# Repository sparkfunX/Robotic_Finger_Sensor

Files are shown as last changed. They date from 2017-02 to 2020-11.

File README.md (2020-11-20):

Robotic Finger Sensor 
========================

Robotic Finger Sensor

Robotic Finger Sensor  

[*Robotic Finger Sensor (SPX-14200)*](https://www.sparkfun.com/products/14200)  

[*Robotic Finger Sensor v2 (SPX-14687)*](https://www.sparkfun.com/products/14687)

A robotic finger sensor capable of detecting very light touches. Uses the VCNL4040 IR distance sensor. 

Repository Contents
------------------

* **/Firmware** - Example Arduino sketch to demostrate how to read from the various sensors.
* **/Hardware** - All the Eagle PCB design files (.brd, .sch). MOld files are included as well. 

License Information
-------------------

This product is _**open source**_! 

Please review the LICENSE.md file for license information. 

If you have any questions or concerns on licensing, please contact technical support on our [SparkFun forums](https://forum.sparkfun.com/viewforum.php?f=152).

Distributed as-is; no warranty is given.

- Your friends at SparkFun.

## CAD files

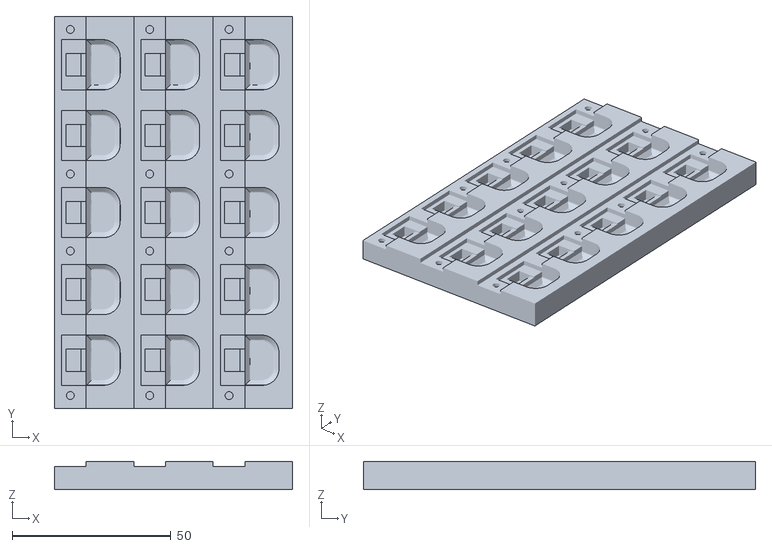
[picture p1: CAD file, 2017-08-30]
Hardware/MOLD/FingerMoldIceCubeProduction_Reduced_depth.stl
75.0 x 123.5 x 8.89

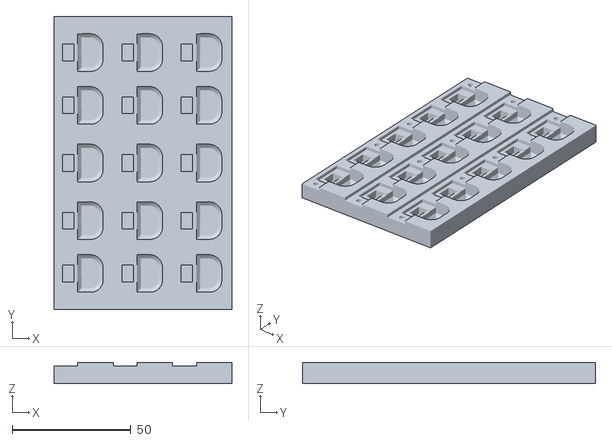
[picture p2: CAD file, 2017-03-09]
Hardware/MOLD/FingerMoldIceCubeProduction.stl
75.0 x 123.5 x 8.89

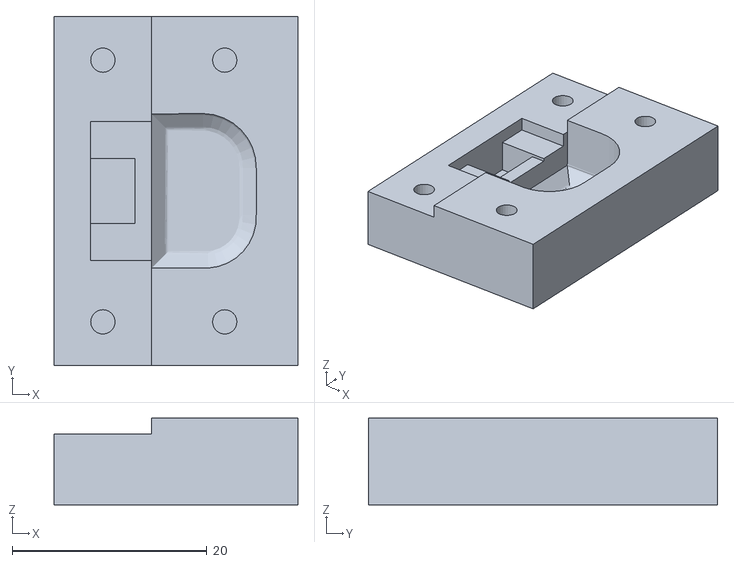
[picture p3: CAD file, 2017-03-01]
Hardware/MOLD/FingerMoldIceCube.stl
25.0 x 35.8 x 8.89

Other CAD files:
Hardware/MOLD/FingerMoldIceCube.skp
Hardware/MOLD/FingerMoldIceCubeProduction.skp
Hardware/MOLD/FingerMoldIceCubeProduction~.skp
Hardware/MOLD/FingerMoldIceCube~.skp

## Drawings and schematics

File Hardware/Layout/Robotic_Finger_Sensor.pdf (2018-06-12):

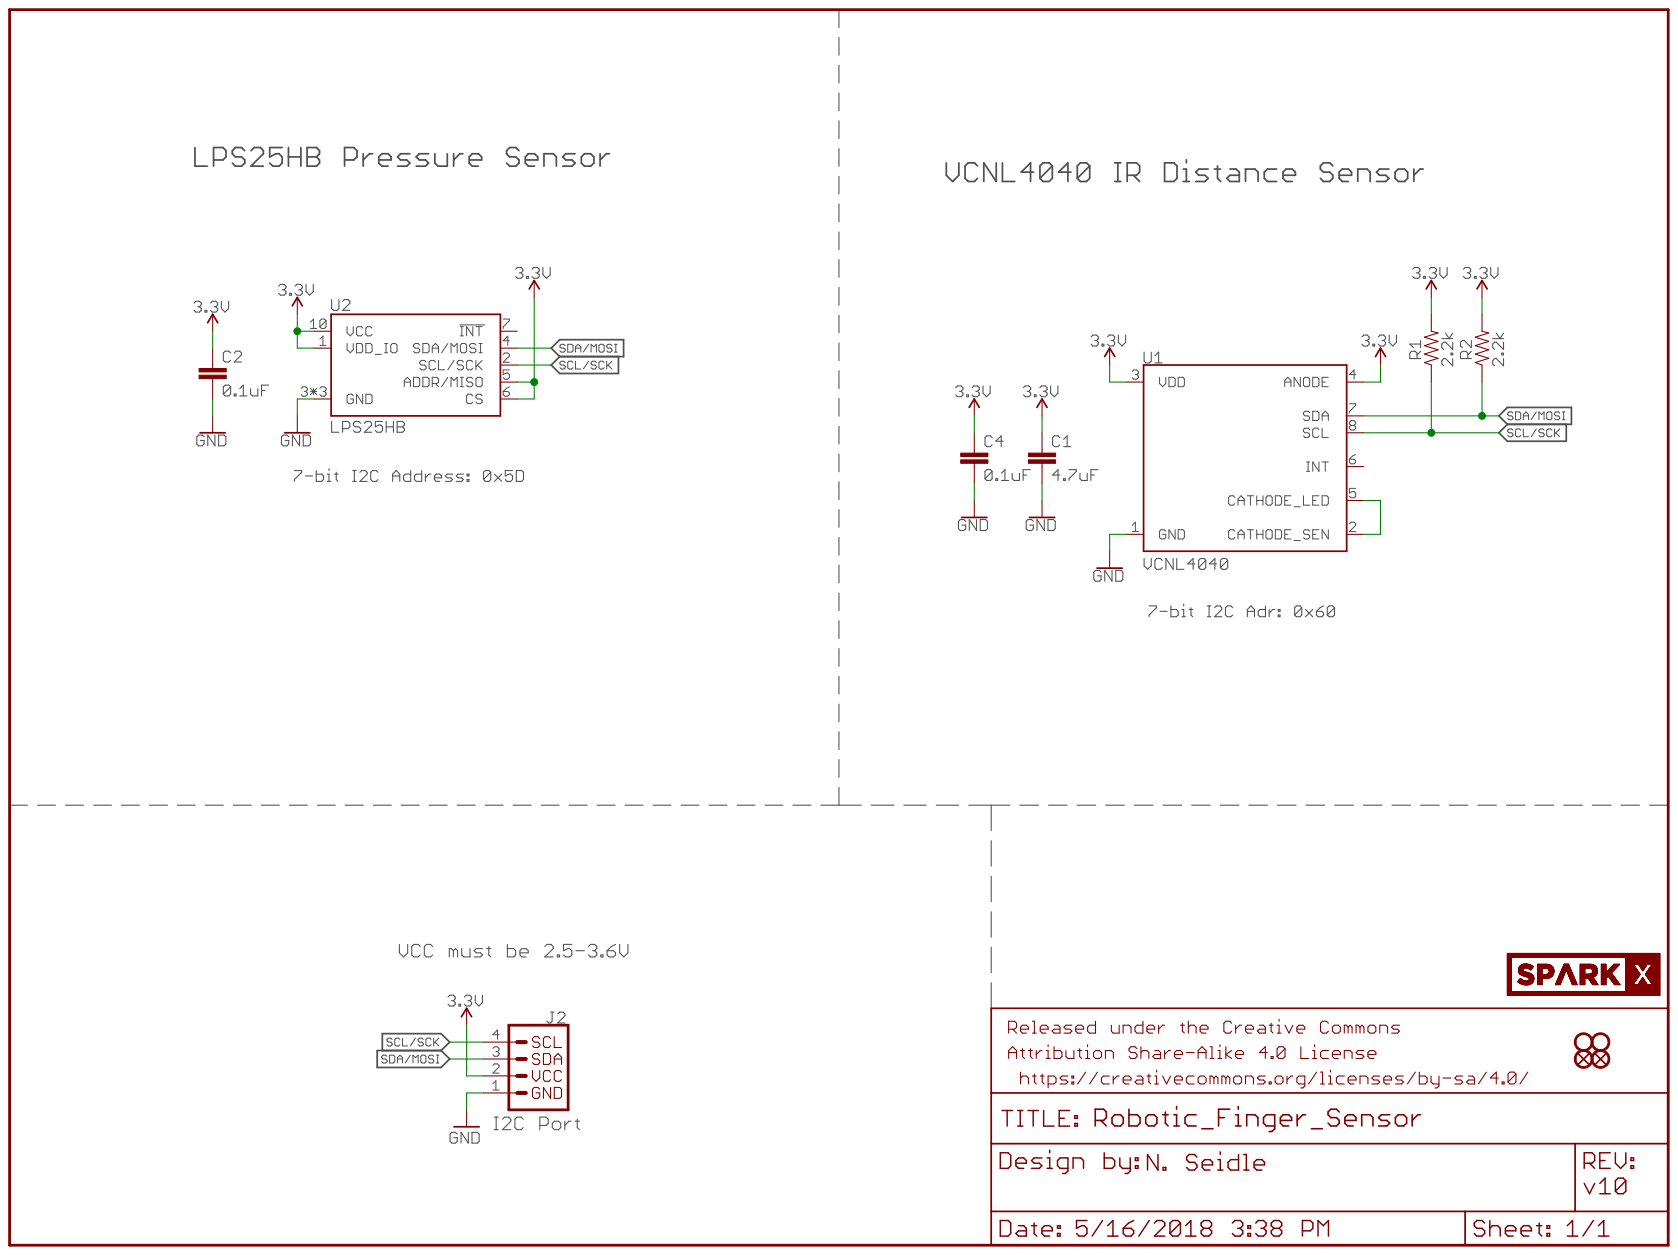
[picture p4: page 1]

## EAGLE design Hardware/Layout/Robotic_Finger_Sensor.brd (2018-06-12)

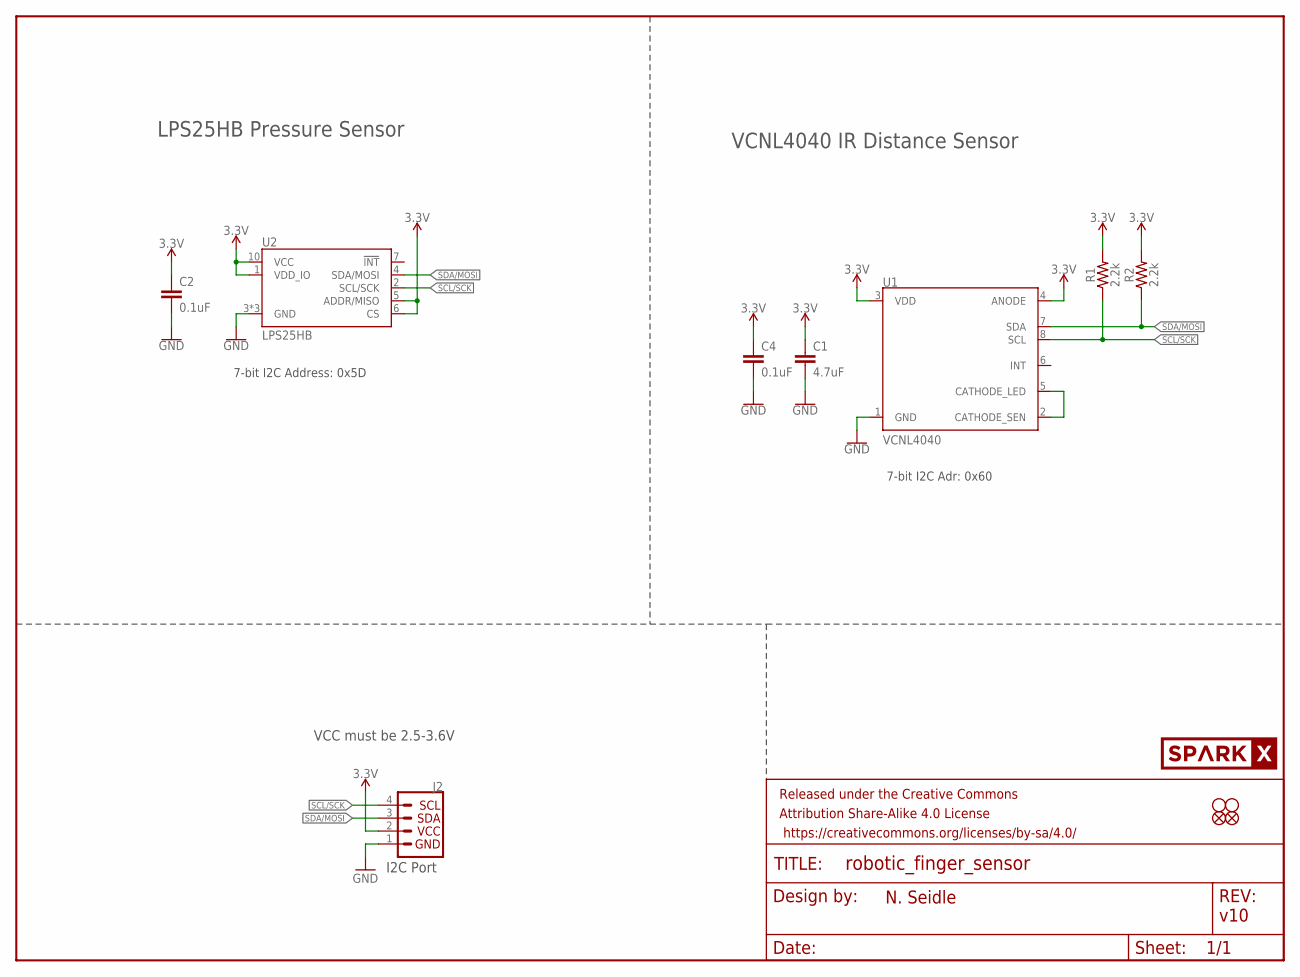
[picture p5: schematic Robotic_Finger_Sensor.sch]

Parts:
C1: 4.7uF; 0603
C2, C4: 0.1uF; 0603
FD1, FD2: FIDUCIALUFIDUCIAL; FIDUCIAL-MICRO
FRAME2: FRAME-LETTER; CREATIVE_COMMONS
J2: I2C_STANDARDJS-1MM; 1X04_1MM_RA
R1, R2: 2.2k; 0603
U1: VCNL4040
U2: LPS25HB
U$2: SPARKX-LOGO3; SPARKX-SMALL
U$3, U$4: STAND-OFF; STAND-OFF-#2

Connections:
3.3V: C1.1, C2.1, C4.1, J2.2 (VCC), R1.2, R2.2, U1.3 (VDD), U1.4 (ANODE), U2.1 (VDD_IO), U2.5 (ADDR/MISO), U2.6 (CS), U2.10 (VCC)
GND: C1.2, C2.2, C4.2, J2.1 (GND), U1.1 (GND), U2.3 (GND), U2.8 (GND), U2.9 (GND)
unnamed: U1.2 (CATHODE_SEN), U1.5 (CATHODE_LED)
SCL/SCK: J2.4 (SCL), R1.1, U1.8 (SCL), U2.2 (SCL/SCK)
SDA/MOSI: J2.3 (SDA), R2.1, U1.7 (SDA), U2.4 (SDA/MOSI)

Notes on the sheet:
v10
N. Seidle
VCNL4040 IR Distance Sensor
VCC must be 2.5-3.6V
I2C Port
7-bit I2C Adr: 0x60
LPS25HB Pressure Sensor
7-bit I2C Address: 0x5D

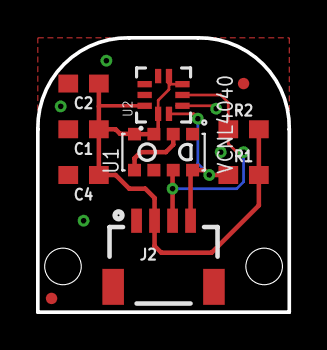
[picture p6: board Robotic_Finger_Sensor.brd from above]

Board: 2 copper layers, 14.0 x 15.2 mm, 18 parts (5 on the bottom side), 5 nets.

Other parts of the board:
U$6: ROBOTIC0
U$7: SENSOR2
U$9: FINGER0
U$11: (QWIIC)

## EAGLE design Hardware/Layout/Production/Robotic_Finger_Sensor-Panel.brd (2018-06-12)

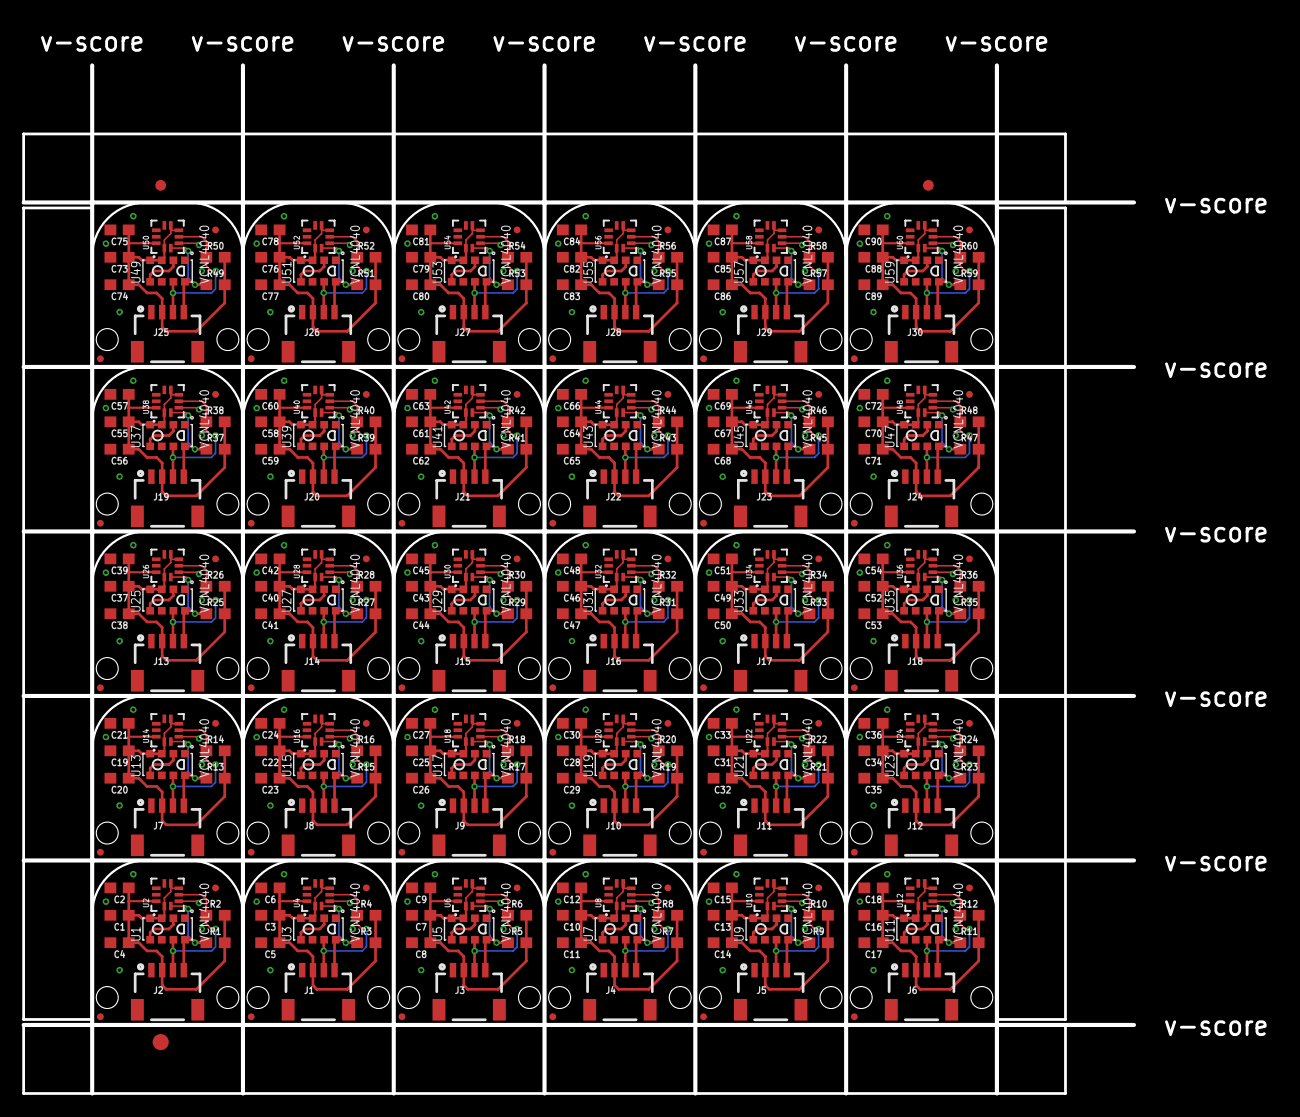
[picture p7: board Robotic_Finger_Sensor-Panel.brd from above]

Board: 2 copper layers, 102.9 x 95.2 mm, 513 parts (150 on the bottom side), 150 nets.

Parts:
C1, C3, C7, C10, C13, C16, C19, C22, C25, C28, C31, C34, C37, C40, C43, C46, C49, C52, C55, C58, C61, C64, C67, C70, C73, C76, C79, C82, C85, C88: 4.7uF; 0603
C2, C4, C5, C6, C8, C9, C11, C12, C14, C15, C17, C18, C20, C21, C23, C24, C26, C27, C29, C30, C32, C33, C35, C36, C38, C39, C41, C42, C44, C45, C47, C48, C50, C51, C53, C54, C56, C57, C59, C60, C62, C63, C65, C66, C68, C69, C71, C72, C74, C75, C77, C78, C80, C81, C83, C84, C86, C87, C89, C90: 0.1uF; 0603
E$1, E$2: FIDUCIAL-1X2
E$3: FIDUCIAL-1.5X3
FD1, FD2, FD3, FD4, FD5, FD6, FD7, FD8, FD9, FD10, FD11, FD12, FD13, FD14, FD15, FD16, FD17, FD18, FD19, FD20, FD21, FD22, FD23, FD24, FD25, FD26, FD27, FD28, FD29, FD30, FD31, FD32, FD33, FD34, FD35, FD36, FD37, FD38, FD39, FD40, FD41, FD42, FD43, FD44, FD45, FD46, FD47, FD48, FD49, FD50, FD51, FD52, FD53, FD54, FD55, FD56, FD57, FD58, FD59, FD60: FIDUCIALUFIDUCIAL; FIDUCIAL-MICRO
J1, J2, J3, J4, J5, J6, J7, J8, J9, J10, J11, J12, J13, J14, J15, J16, J17, J18, J19, J20, J21, J22, J23, J24, J25, J26, J27, J28, J29, J30: 1X04_1MM_RA
R1, R2, R3, R4, R5, R6, R7, R8, R9, R10, R11, R12, R13, R14, R15, R16, R17, R18, R19, R20, R21, R22, R23, R24, R25, R26, R27, R28, R29, R30, R31, R32, R33, R34, R35, R36, R37, R38, R39, R40, R41, R42, R43, R44, R45, R46, R47, R48, R49, R50, R51, R52, R53, R54, R55, R56, R57, R58, R59, R60: 2.2k; 0603
U1, U3, U5, U7, U9, U11, U13, U15, U17, U19, U21, U23, U25, U27, U29, U31, U33, U35, U37, U39, U41, U43, U45, U47, U49, U51, U53, U55, U57, U59: VCNL4040
U2, U4, U6, U8, U10, U12, U14, U16, U18, U20, U22, U24, U26, U28, U30, U32, U34, U36, U38, U40, U42, U44, U46, U48, U50, U52, U54, U56, U58, U60: LPS25HB
U$1, U$2, U$15, U$22, U$29, U$36, U$43, U$50, U$57, U$64, U$71, U$78, U$85, U$92, U$99, U$106, U$113, U$120, U$127, U$134, U$141, U$148, U$155, U$162, U$169, U$176, U$183, U$190, U$197, U$204: SPARKX-LOGO3; SPARKX-SMALL
U$3, U$4, U$5, U$8, U$16, U$17, U$23, U$24, U$30, U$31, U$37, U$38, U$44, U$45, U$51, U$52, U$58, U$59, U$65, U$66, U$72, U$73, U$79, U$80, U$86, U$87, U$93, U$94, U$100, U$101, U$107, U$108, U$114, U$115, U$121, U$122, U$128, U$129, U$135, U$136, U$142, U$143, U$149, U$150, U$156, U$157, U$163, U$164, U$170, U$171, U$177, U$178, U$184, U$185, U$191, U$192, U$198, U$199, U$205, U$206: STAND-OFF; STAND-OFF-#2
U$6, U$12, U$19, U$26, U$33, U$40, U$47, U$54, U$61, U$68, U$75, U$82, U$89, U$96, U$103, U$110, U$117, U$124, U$131, U$138, U$145, U$152, U$159, U$166, U$173, U$180, U$187, U$194, U$201, U$208: ROBOTIC0
U$7, U$13, U$20, U$27, U$34, U$41, U$48, U$55, U$62, U$69, U$76, U$83, U$90, U$97, U$104, U$111, U$118, U$125, U$132, U$139, U$146, U$153, U$160, U$167, U$174, U$181, U$188, U$195, U$202, U$209: SENSOR2
U$9, U$14, U$21, U$28, U$35, U$42, U$49, U$56, U$63, U$70, U$77, U$84, U$91, U$98, U$105, U$112, U$119, U$126, U$133, U$140, U$147, U$154, U$161, U$168, U$175, U$182, U$189, U$196, U$203, U$210: FINGER0
U$10, U$11, U$18, U$25, U$32, U$39, U$46, U$53, U$60, U$67, U$74, U$81, U$88, U$95, U$102, U$109, U$116, U$123, U$130, U$137, U$144, U$151, U$158, U$165, U$172, U$179, U$186, U$193, U$200, U$207: (QWIIC)

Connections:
3.3V: C1.1, C2.1, C4.1, J2.2, R1.2, R2.2, U1.3, U1.4, U2.1, U2.5, U2.6, U2.10
3.3V1: C3.1, C5.1, C6.1, J1.2, R3.2, R4.2, U3.3, U3.4, U4.1, U4.5, U4.6, U4.10
3.3V2: C7.1, C8.1, C9.1, J3.2, R5.2, R6.2, U5.3, U5.4, U6.1, U6.5, U6.6, U6.10
3.3V3: C10.1, C11.1, C12.1, J4.2, R7.2, R8.2, U7.3, U7.4, U8.1, U8.5, U8.6, U8.10
3.3V4: C13.1, C14.1, C15.1, J5.2, R9.2, R10.2, U9.3, U9.4, U10.1, U10.5, U10.6, U10.10
3.3V5: C16.1, C17.1, C18.1, J6.2, R11.2, R12.2, U11.3, U11.4, U12.1, U12.5, U12.6, U12.10
3.3V6: C19.1, C20.1, C21.1, J7.2, R13.2, R14.2, U13.3, U13.4, U14.1, U14.5, U14.6, U14.10
3.3V7: C22.1, C23.1, C24.1, J8.2, R15.2, R16.2, U15.3, U15.4, U16.1, U16.5, U16.6, U16.10
3.3V8: C25.1, C26.1, C27.1, J9.2, R17.2, R18.2, U17.3, U17.4, U18.1, U18.5, U18.6, U18.10
3.3V9: C28.1, C29.1, C30.1, J10.2, R19.2, R20.2, U19.3, U19.4, U20.1, U20.5, U20.6, U20.10
3.3V10: C31.1, C32.1, C33.1, J11.2, R21.2, R22.2, U21.3, U21.4, U22.1, U22.5, U22.6, U22.10
3.3V11: C34.1, C35.1, C36.1, J12.2, R23.2, R24.2, U23.3, U23.4, U24.1, U24.5, U24.6, U24.10
3.3V12: C37.1, C38.1, C39.1, J13.2, R25.2, R26.2, U25.3, U25.4, U26.1, U26.5, U26.6, U26.10
3.3V13: C40.1, C41.1, C42.1, J14.2, R27.2, R28.2, U27.3, U27.4, U28.1, U28.5, U28.6, U28.10
3.3V14: C43.1, C44.1, C45.1, J15.2, R29.2, R30.2, U29.3, U29.4, U30.1, U30.5, U30.6, U30.10
3.3V15: C46.1, C47.1, C48.1, J16.2, R31.2, R32.2, U31.3, U31.4, U32.1, U32.5, U32.6, U32.10
3.3V16: C49.1, C50.1, C51.1, J17.2, R33.2, R34.2, U33.3, U33.4, U34.1, U34.5, U34.6, U34.10
3.3V17: C52.1, C53.1, C54.1, J18.2, R35.2, R36.2, U35.3, U35.4, U36.1, U36.5, U36.6, U36.10
3.3V18: C55.1, C56.1, C57.1, J19.2, R37.2, R38.2, U37.3, U37.4, U38.1, U38.5, U38.6, U38.10
3.3V19: C58.1, C59.1, C60.1, J20.2, R39.2, R40.2, U39.3, U39.4, U40.1, U40.5, U40.6, U40.10
3.3V20: C61.1, C62.1, C63.1, J21.2, R41.2, R42.2, U41.3, U41.4, U42.1, U42.5, U42.6, U42.10
3.3V21: C64.1, C65.1, C66.1, J22.2, R43.2, R44.2, U43.3, U43.4, U44.1, U44.5, U44.6, U44.10
3.3V22: C67.1, C68.1, C69.1, J23.2, R45.2, R46.2, U45.3, U45.4, U46.1, U46.5, U46.6, U46.10
3.3V23: C70.1, C71.1, C72.1, J24.2, R47.2, R48.2, U47.3, U47.4, U48.1, U48.5, U48.6, U48.10
3.3V24: C73.1, C74.1, C75.1, J25.2, R49.2, R50.2, U49.3, U49.4, U50.1, U50.5, U50.6, U50.10
3.3V25: C76.1, C77.1, C78.1, J26.2, R51.2, R52.2, U51.3, U51.4, U52.1, U52.5, U52.6, U52.10
3.3V26: C79.1, C80.1, C81.1, J27.2, R53.2, R54.2, U53.3, U53.4, U54.1, U54.5, U54.6, U54.10
3.3V27: C82.1, C83.1, C84.1, J28.2, R55.2, R56.2, U55.3, U55.4, U56.1, U56.5, U56.6, U56.10
3.3V28: C85.1, C86.1, C87.1, J29.2, R57.2, R58.2, U57.3, U57.4, U58.1, U58.5, U58.6, U58.10
3.3V29: C88.1, C89.1, C90.1, J30.2, R59.2, R60.2, U59.3, U59.4, U60.1, U60.5, U60.6, U60.10
GND: C1.2, C2.2, C4.2, J2.1, U1.1, U2.3, U2.8, U2.9
GND1: C3.2, C5.2, C6.2, J1.1, U3.1, U4.3, U4.8, U4.9
GND2: C7.2, C8.2, C9.2, J3.1, U5.1, U6.3, U6.8, U6.9
GND3: C10.2, C11.2, C12.2, J4.1, U7.1, U8.3, U8.8, U8.9
GND4: C13.2, C14.2, C15.2, J5.1, U9.1, U10.3, U10.8, U10.9
GND5: C16.2, C17.2, C18.2, J6.1, U11.1, U12.3, U12.8, U12.9
GND6: C19.2, C20.2, C21.2, J7.1, U13.1, U14.3, U14.8, U14.9
GND7: C22.2, C23.2, C24.2, J8.1, U15.1, U16.3, U16.8, U16.9
GND8: C25.2, C26.2, C27.2, J9.1, U17.1, U18.3, U18.8, U18.9
GND9: C28.2, C29.2, C30.2, J10.1, U19.1, U20.3, U20.8, U20.9
GND10: C31.2, C32.2, C33.2, J11.1, U21.1, U22.3, U22.8, U22.9
GND11: C34.2, C35.2, C36.2, J12.1, U23.1, U24.3, U24.8, U24.9
GND12: C37.2, C38.2, C39.2, J13.1, U25.1, U26.3, U26.8, U26.9
GND13: C40.2, C41.2, C42.2, J14.1, U27.1, U28.3, U28.8, U28.9
GND14: C43.2, C44.2, C45.2, J15.1, U29.1, U30.3, U30.8, U30.9
GND15: C46.2, C47.2, C48.2, J16.1, U31.1, U32.3, U32.8, U32.9
GND16: C49.2, C50.2, C51.2, J17.1, U33.1, U34.3, U34.8, U34.9
GND17: C52.2, C53.2, C54.2, J18.1, U35.1, U36.3, U36.8, U36.9
GND18: C55.2, C56.2, C57.2, J19.1, U37.1, U38.3, U38.8, U38.9
GND19: C58.2, C59.2, C60.2, J20.1, U39.1, U40.3, U40.8, U40.9
GND20: C61.2, C62.2, C63.2, J21.1, U41.1, U42.3, U42.8, U42.9
GND21: C64.2, C65.2, C66.2, J22.1, U43.1, U44.3, U44.8, U44.9
GND22: C67.2, C68.2, C69.2, J23.1, U45.1, U46.3, U46.8, U46.9
GND23: C70.2, C71.2, C72.2, J24.1, U47.1, U48.3, U48.8, U48.9
GND24: C73.2, C74.2, C75.2, J25.1, U49.1, U50.3, U50.8, U50.9
GND25: C76.2, C77.2, C78.2, J26.1, U51.1, U52.3, U52.8, U52.9
GND26: C79.2, C80.2, C81.2, J27.1, U53.1, U54.3, U54.8, U54.9
GND27: C82.2, C83.2, C84.2, J28.1, U55.1, U56.3, U56.8, U56.9
GND28: C85.2, C86.2, C87.2, J29.1, U57.1, U58.3, U58.8, U58.9
GND29: C88.2, C89.2, C90.2, J30.1, U59.1, U60.3, U60.8, U60.9
unnamed: U1.2, U1.5
unnamed: U3.2, U3.5
unnamed: U5.2, U5.5
unnamed: U7.2, U7.5
unnamed: U9.2, U9.5
unnamed: U11.2, U11.5
unnamed: U13.2, U13.5
unnamed: U15.2, U15.5
unnamed: U17.2, U17.5
unnamed: U19.2, U19.5
unnamed: U21.2, U21.5
unnamed: U23.2, U23.5
unnamed: U25.2, U25.5
unnamed: U27.2, U27.5
unnamed: U29.2, U29.5
unnamed: U31.2, U31.5
unnamed: U33.2, U33.5
unnamed: U35.2, U35.5
unnamed: U37.2, U37.5
unnamed: U39.2, U39.5
unnamed: U41.2, U41.5
unnamed: U43.2, U43.5
unnamed: U45.2, U45.5
unnamed: U47.2, U47.5
unnamed: U49.2, U49.5
unnamed: U51.2, U51.5
unnamed: U53.2, U53.5
unnamed: U55.2, U55.5
unnamed: U57.2, U57.5
unnamed: U59.2, U59.5
SCL/SCK: J2.4, R1.1, U1.8, U2.2
SCL/SCK1: J1.4, R3.1, U3.8, U4.2
SCL/SCK2: J3.4, R5.1, U5.8, U6.2
SCL/SCK3: J4.4, R7.1, U7.8, U8.2
SCL/SCK4: J5.4, R9.1, U9.8, U10.2
SCL/SCK5: J6.4, R11.1, U11.8, U12.2
SCL/SCK6: J7.4, R13.1, U13.8, U14.2
SCL/SCK7: J8.4, R15.1, U15.8, U16.2
SCL/SCK8: J9.4, R17.1, U17.8, U18.2
SCL/SCK9: J10.4, R19.1, U19.8, U20.2
SCL/SCK10: J11.4, R21.1, U21.8, U22.2
SCL/SCK11: J12.4, R23.1, U23.8, U24.2
SCL/SCK12: J13.4, R25.1, U25.8, U26.2
SCL/SCK13: J14.4, R27.1, U27.8, U28.2
SCL/SCK14: J15.4, R29.1, U29.8, U30.2
SCL/SCK15: J16.4, R31.1, U31.8, U32.2
SCL/SCK16: J17.4, R33.1, U33.8, U34.2
SCL/SCK17: J18.4, R35.1, U35.8, U36.2
SCL/SCK18: J19.4, R37.1, U37.8, U38.2
SCL/SCK19: J20.4, R39.1, U39.8, U40.2
SCL/SCK20: J21.4, R41.1, U41.8, U42.2
SCL/SCK21: J22.4, R43.1, U43.8, U44.2
SCL/SCK22: J23.4, R45.1, U45.8, U46.2
SCL/SCK23: J24.4, R47.1, U47.8, U48.2
SCL/SCK24: J25.4, R49.1, U49.8, U50.2
SCL/SCK25: J26.4, R51.1, U51.8, U52.2
SCL/SCK26: J27.4, R53.1, U53.8, U54.2
SCL/SCK27: J28.4, R55.1, U55.8, U56.2
SCL/SCK28: J29.4, R57.1, U57.8, U58.2
SCL/SCK29: J30.4, R59.1, U59.8, U60.2
SDA/MOSI: J2.3, R2.1, U1.7, U2.4
SDA/MOSI1: J1.3, R4.1, U3.7, U4.4
SDA/MOSI2: J3.3, R6.1, U5.7, U6.4
SDA/MOSI3: J4.3, R8.1, U7.7, U8.4
SDA/MOSI4: J5.3, R10.1, U9.7, U10.4
SDA/MOSI5: J6.3, R12.1, U11.7, U12.4
SDA/MOSI6: J7.3, R14.1, U13.7, U14.4
SDA/MOSI7: J8.3, R16.1, U15.7, U16.4
SDA/MOSI8: J9.3, R18.1, U17.7, U18.4
SDA/MOSI9: J10.3, R20.1, U19.7, U20.4
SDA/MOSI10: J11.3, R22.1, U21.7, U22.4
SDA/MOSI11: J12.3, R24.1, U23.7, U24.4
SDA/MOSI12: J13.3, R26.1, U25.7, U26.4
SDA/MOSI13: J14.3, R28.1, U27.7, U28.4
SDA/MOSI14: J15.3, R30.1, U29.7, U30.4
SDA/MOSI15: J16.3, R32.1, U31.7, U32.4
SDA/MOSI16: J17.3, R34.1, U33.7, U34.4
SDA/MOSI17: J18.3, R36.1, U35.7, U36.4
SDA/MOSI18: J19.3, R38.1, U37.7, U38.4
SDA/MOSI19: J20.3, R40.1, U39.7, U40.4
SDA/MOSI20: J21.3, R42.1, U41.7, U42.4
SDA/MOSI21: J22.3, R44.1, U43.7, U44.4
SDA/MOSI22: J23.3, R46.1, U45.7, U46.4
SDA/MOSI23: J24.3, R48.1, U47.7, U48.4
SDA/MOSI24: J25.3, R50.1, U49.7, U50.4
SDA/MOSI25: J26.3, R52.1, U51.7, U52.4
SDA/MOSI26: J27.3, R54.1, U53.7, U54.4
SDA/MOSI27: J28.3, R56.1, U55.7, U56.4
SDA/MOSI28: J29.3, R58.1, U57.7, U58.4
SDA/MOSI29: J30.3, R60.1, U59.7, U60.4

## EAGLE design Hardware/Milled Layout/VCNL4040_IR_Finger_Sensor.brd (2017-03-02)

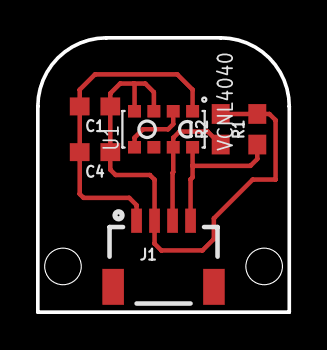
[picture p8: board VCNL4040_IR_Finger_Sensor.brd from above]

Board: 2 copper layers, 14.0 x 15.2 mm, 9 parts (0 on the bottom side), 5 nets.

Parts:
C1: 2.2uF; 0603
C4: 0.1uF; 0603
FRAME2: FRAME-LETTER; CREATIVE_COMMONS
J1: 1X04_1MM_RA
R1, R2: 2.2k; 0603
U1: VCNL4040
U$1, U$2: STAND-OFF; STAND-OFF-#2

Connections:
3.3V: C1.1, C4.1, J1.2, R1.2, R2.2, U1.3, U1.4
GND: C1.2, C4.2, J1.1, U1.1
unnamed: U1.2, U1.5
SCL: J1.4, R1.1, U1.8
SDA: J1.3, R2.1, U1.7

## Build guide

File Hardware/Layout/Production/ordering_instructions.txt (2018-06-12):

panel size, 97x89mm
PCB thickness, 1.6mm
number of layers, 2
soldermask color, Black
silkscreen color, White
oz copper, 1oz
finish, HASL lead free
stencils, top+bottom
pcs per panel, 30

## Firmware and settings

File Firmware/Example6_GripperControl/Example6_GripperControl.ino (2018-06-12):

/*
  Robotic Finger Sensor - Sensing a touch and controlling a gripper
  By: Nathan Seidle
  SparkFun Electronics
  Date: June 12th, 2018
  License: This software is open source and can be used for any purpose.

  This code identifies touch/release events and controls (stops) a servo to create a robotic gripper with light grip,
  on most any sized/shaped object.

  Open a terminal window at 9600 and view the state as you touch the sensor.
  Press 'z' or 'c' to begin closing the servo. Stops (plus a small grip amount) when touch is detected.

  This code was designed to work with an Arduino Uno but should work nicely with Teensy and others.

  Brought to you by SparkFun (orignial code), the Correll Lab at the University
  of Colorado, Boulder and Robotic Materials Inc.
*/

#include <Servo.h>
Servo gripperServo;

#include <Wire.h> //For Arduino Uno
//#include <i2c_t3.h> //Use <i2c_t3.h> for Teensy

#include "SparkFun_VCNL4040_Arduino_Library.h" //Library: http://librarymanager/All#SparkFun_VCNL4040
VCNL4040 proximitySensor;

#include "SparkFun_LPS25HB_Arduino_Library.h"  //Library: http://librarymanager/All#SparkFun_LPS25HB
LPS25HB pressureSensor;

#include <math.h>

const byte servo = 9; //Attach servo PWM pin here. Any PWM pin is ok.
const byte button = 7; //Press the button, cause gripper to close or open

#define LOOP_TIME 10  // loop duration in ms

// Touch/release detection
#define EA 0.3  // exponential average weight parameter / cut-off frequency for high-pass filter

/***** GLOBAL VARIABLES *****/
unsigned int proximity_value; // current proximity reading
unsigned int average_value;   // low-pass filtered proximity reading
signed int fa2;              // FA-II value;
signed int sensitivity = 100;  // Sensitivity of touch/release detection, values closer to zero increase sensitivity

boolean movement = true; //Keeps track of if we are sensing movement or not
byte noMovementCounts = 0; //Keeps track of no movement detected from sensor

byte gripperState = 0; //Statemachine variable
#define STATE_OPEN 0
#define STATE_CLOSED 1
#define STATE_OPENING 2
#define STATE_CLOSING 3
#define STATE_STOPPED 4
#define STATE_CONTACT 5

byte touchState = 0; //Statemachine variable
#define NOT_TOUCHING 0
#define TOUCHING 1

int servoPosition = 150; //Keeps track of where the servo is currently at
const byte servoOpenPosition = 150; //Max open gripper position
//const byte servoClosedPosition = 65; //Min closed gripper position
const byte servoClosedPosition = 25; //For testing
const byte closingRate = 1; //Rate at which to close the servo. Setting too high risks servo putting too much pressure before sensing touch
const byte openingRate = 100; //Rate at which to open the servo. Can be large.
const byte gripAmount = 5; //Additional servo position from contact point to get grip

void setup()
{
  Serial.begin(9600);
  Serial.println("Robotic Finger Sensor v2 Example");

  Wire.begin();
  Wire.setClock(400000); //Increase I2C bus speed to 400kHz

  if (proximitySensor.begin() == false)
  {
    Serial.println("Proximity sensor not found. Please check wiring.");
    while (1); //Freeze!
  }
  
  pressureSensor.begin();
  if(pressureSensor.isConnected() == false)  // The library supports some different error codes such as "DISCONNECTED"
  {
    Serial.println("Pressure sensor not found. Please check wiring.");
    while (1); //Freeze!
  }

  pinMode(button, INPUT_PULLUP);

  //Setup servo
  gripperServo.attach(servo);
  gripperServo.write(servoOpenPosition); //Goto the resting position (gripper open)
  gripperState = STATE_OPEN;
  servoPosition = servoOpenPosition;
  touchState = NOT_TOUCHING;

  //Setup initial values
  average_value = proximitySensor.getProximity(); //Get proximity values
  fa2 = 0;
}

void loop()
{
  unsigned long startTime = millis();

  if(digitalRead(button) == LOW)
  {
    delay(50); //Debounce
    while(digitalRead(button) == LOW) delay(1); //Wait for user to stop pressing button
    
    if (touchState == TOUCHING) gripperState = STATE_OPENING;
    else if(gripperState == STATE_CLOSING) gripperState = STATE_OPENING;
    else if(gripperState == STATE_OPEN) gripperState = STATE_CLOSING;
    else if(gripperState == STATE_CLOSED) gripperState = STATE_OPENING;
    else if(gripperState == STATE_OPENING && touchState != TOUCHING) gripperState = STATE_CLOSING;
    else gripperState = STATE_OPENING;
  }

  if (Serial.available())
  {
    byte incoming = Serial.read();
    if (incoming == 'c' || incoming == 'z')
    {
      //Don't keep closing if we're touching
      if (touchState != TOUCHING) gripperState = STATE_CLOSING;
    }
    else if (incoming == 'o' || incoming == 'a')
    {
      gripperState = STATE_OPENING;
    }
  }

  proximity_value = proximitySensor.getProximity(); //Get proximity values
  fa2 = (signed int) average_value - proximity_value;

  //Serial.print(proximity_value);
  //Serial.print(",");
  //Serial.print(fa2);
  //Serial.print(",");

  if (fa2 > sensitivity && movement == false)
  {
    movement = true;
    noMovementCounts = 0;
    Serial.println("R");
    touchState = NOT_TOUCHING;

    //If needed, put code here to re-close the gripper to maintain grip
  }
  else if (fa2 < -sensitivity && movement == false)
  {
    if (gripperState == STATE_CLOSING)
    {
      //Contact! Continue closing for some grip
      gripperState = STATE_CONTACT;
    }

    movement = true;
    noMovementCounts = 0;
    Serial.println("T");
    touchState = TOUCHING;
  }

  //See if there is no movement detected
  if (abs(fa2) < 5)
  {
    noMovementCounts++;
    if (noMovementCounts > 2) movement = false;
    if (noMovementCounts > 100) noMovementCounts = 100; //Limit variable so no overflow
  }

  //See if we have a proximity that is too large, then we aren't touching
  if(proximity_value < 200)
  {
    touchState = NOT_TOUCHING;
  }

  if (gripperState == STATE_CLOSING)
  {
    Serial.println("Closing");
    servoPosition -= closingRate;
    if (servoPosition <= servoClosedPosition)
    {
      gripperState = STATE_CLOSED;
      servoPosition = servoClosedPosition;
    }

    gripperServo.write(servoPosition); //Adjust the servo closed
  }
  else if (gripperState == STATE_OPENING)
  {
    Serial.println("Opening");
    servoPosition += openingRate;
    if (servoPosition >= servoOpenPosition)
    {
      gripperState = STATE_OPEN;
      servoPosition = servoOpenPosition;
    }

    gripperServo.write(servoPosition); //Adjust the servo open
  }
  else if (gripperState == STATE_CONTACT)
  {
    Serial.println("Contact!");
    servoPosition -= gripAmount; //Move servo a little more to get grip
    gripperServo.write(servoPosition); //Adjust the servo open
    delay(10); //Wait for servo to get there

    gripperState = STATE_STOPPED;
  }

  //Print all the things
  Serial.print("ServoPosition: ");
  Serial.print(servoPosition);

  Serial.print(" State: ");
  if (gripperState == STATE_OPEN) Serial.print("Open");
  else if (gripperState == STATE_CLOSED) Serial.print("Closed");
  else if (gripperState == STATE_OPENING) Serial.print("Opening");
  else if (gripperState == STATE_CLOSING) Serial.print("Closing");
  else if (gripperState == STATE_STOPPED) Serial.print("Stopped");

  if (touchState == NOT_TOUCHING) Serial.print(" Not Touching");
  else if (touchState == TOUCHING) Serial.print(" Touching");

  Serial.print(" Prox: ");
  Serial.print(proximity_value);

  Serial.println();

  //Do this last
  average_value = EA * proximity_value + (1 - EA) * average_value;
  while (millis() < startTime + LOOP_TIME); // enforce constant loop time
}

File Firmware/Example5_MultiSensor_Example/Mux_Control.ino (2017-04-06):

/*
 Basic control and commands for the PCA9548A/TCA9548A I2C multiplexer
*/

#define MUX_ADDR 0x70 //7-bit unshifted default I2C Address

//Enables a specific port number
boolean enableMuxPort(byte portNumber)
{
  if(portNumber > 7) portNumber = 7;

  //Read the current mux settings
  Wire.requestFrom(MUX_ADDR, 1);
  if(!Wire.available()) return(false); //Error
  byte settings = Wire.read();

  //Set the wanted bit to enable the port
  settings |= (1 << portNumber);

  Wire.beginTransmission(MUX_ADDR);
  Wire.write(settings);
  Wire.endTransmission();

  return(true);
}

//Disables a specific port number
boolean disableMuxPort(byte portNumber)
{
  if(portNumber > 7) portNumber = 7;

  //Read the current mux settings
  Wire.requestFrom(MUX_ADDR, 1);
  if(!Wire.available()) return(false); //Error
  byte settings = Wire.read();

  //Clear the wanted bit to disable the port
  settings &= ~(1 << portNumber);

  Wire.beginTransmission(MUX_ADDR);
  Wire.write(settings);
  Wire.endTransmission();

  return(true);
}

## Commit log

2017-02-07 Adding folder structure
    [VCNL4040_IR_Finger_Sensor.brd, VCNL4040_IR_Finger_Sensor.sch]
2017-02-08 Finished Schematic
    [VCNL4040_IR_Finger_Sensor.brd, VCNL4040_IR_Finger_Sensor.sch]
2017-02-08 Finished Layout
    [VCNL4040_IR_Finger_Sensor.brd, VCNL4040_IR_Finger_Sensor.sch]
2017-02-08 Added labels to pins
    [VCNL4040_IR_Finger_Sensor.brd]
2017-02-08 Redid Millable version, added Production folder
    [VCNL4040_IR_Finger_Sensor_Production.brd, VCNL4040_IR_Finger_Sensor_Production.sch]
2017-02-08 Expanded Mill version
    [VCNL4040_IR_Finger_Sensor.sch]
2017-02-08 Got rid of INT pin for Mill version
    [VCNL4040_IR_Finger_Sensor.brd, VCNL4040_IR_Finger_Sensor.sch]
2017-02-08 Moved larger board back to origin
    [VCNL4040_IR_Finger_Sensor.brd]
2017-02-08 Added tRestrict under IC
    [VCNL4040_IR_Finger_Sensor.brd]
2017-02-08 Trace cleanup
    [VCNL4040_IR_Finger_Sensor.brd]
2017-02-08 Expanded bottom dimension to remove via
    [VCNL4040_IR_Finger_Sensor.brd]
2017-02-09 New proto layout with no vias
    [VCNL4040_IR_Finger_Sensor.brd, VCNL4040_IR_Finger_Sensor.sch]
2017-02-15 Adding examples. Testing JST on milled layout.
    [VCNL4040_IR_Finger_Sensor.brd, VCNL4040_IR_Finger_Sensor.sch, VCNL4040_IR_Finger_Sensor_Production.brd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]
2017-02-16 Final commit before modifying PCB to match RM's size/shape for molding.
    [VCNL4040_IR_Finger_Sensor.brd]
2017-02-27 Added a comparison sketch to make sure new IC works similarly to original.
    [VCNL4040_IR_Finger_Sensor.brd]
2017-02-28 Extending PCB for molding
    [VCNL4040_IR_Finger_Sensor.brd]
2017-02-28 Moved bed back to origin
    [VCNL4040_IR_Finger_Sensor.brd]
2017-02-28 Adding Mold Top PCB designs for mill
    [MoldTopPCBs.brd]
2017-02-28 Add 3D files to MOLD folder
    [FingerMoldIceCube.skp, FingerMoldIceCube.stl, MoldTopPCBs.brd]
2017-02-28 Adding holes to mold PCB
    [MoldTopPCBs.brd]
2017-02-28 Modifying main mold
    [FingerMoldIceCube.skp, FingerMoldIceCube.stl, FingerMoldIceCube~.skp]
2017-02-28 Changing holes on mold PCB
    [MoldTopPCBs.brd]
2017-02-28 Sketchup changes
    [FingerMoldIceCube.skp, FingerMoldIceCube~.skp]
2017-03-01 Mold update
    [FingerMoldIceCube.skp, FingerMoldIceCube.stl, FingerMoldIceCube~.skp]
2017-03-02 Adding Touch example. Adding HDPE mold test.
2017-03-02 Adding production panel
    [VCNL4040 Panel.GBL, VCNL4040 Panel.GBO, VCNL4040 Panel.GBS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]
2017-03-03 Adding Production model for mold and PCB topper
    [FingerMoldIceCubeProduction.skp, FingerMoldIceCubeProduction.stl, MoldTopPCBProduction.brd]
2017-03-09 Adding too paths for fine finish 1/16" long reach mold.
2017-03-09 Updating mold for production PCBs
    [FingerMoldIceCubeProduction.skp, FingerMoldIceCubeProduction.stl, FingerMoldIceCubeProduction~.skp]
2017-03-09 Adding single version of updated mold.
    [FingerMoldIceCubeProdutctionSingle.skp, FingerMoldIceCubeProdutctionSingle.stl, FingerMoldIceCubeProdutctionSingle~.skp]
2017-03-13 Moved IC towards top of PCB to get more in middle of clear overmold.
2017-03-13 Moved IC up to be more in middle of clear overmolding.
    [VCNL4040_IR_Finger_Sensor_Production.brd]
2017-03-14 Claw control works pretty well.
2017-03-14 Adding PDF schematic
    [Robotic_Finger_Sensor.brd, Robotic_Finger_Sensor.sch, VCNL4040_IR_Finger_Sensor.sch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]
2017-03-15 Added single button control to gripper
2017-03-15 Adding pin silk
    Will be covered by encapsulant but may help
    [Robotic_Finger_Sensor.brd]
2017-03-15 Reduced depth of mold
    [FingerMoldIceCubeProduction.skp, FingerMoldIceCubeProduction_Reduced_depth.stl, FingerMoldIceCubeProduction~.skp]
2017-04-06 Adding multi-finger examples using PCA9548A
2017-08-30 New panel with silk indicators on pins.
    [VCNL4040 Panel.brd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]
2018-04-02 Adding pressure sensor. Cleaning up repo.
    [Robotic_Finger_Sensor.brd, Robotic_Finger_Sensor.sch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]
2018-04-02 Modified footprint silk
    [Robotic_Finger_Sensor-Panel.GBL, Robotic_Finger_Sensor-Panel.GBO, Robotic_Finger_Sensor-Panel.GBS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]
2018-06-05 Update to LPS25HB pressure sensor
    [Robotic_Finger_Sensor-Panel.GBL, Robotic_Finger_Sensor-Panel.GBO, Robotic_Finger_Sensor-Panel.GBS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]
2018-06-12 Updating examples to use modern libraries
    [Robotic_Finger_Sensor-Panel.GBL, Robotic_Finger_Sensor-Panel.GBO, Robotic_Finger_Sensor-Panel.GBS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]
2020-02-18 Change status LED to match Uno

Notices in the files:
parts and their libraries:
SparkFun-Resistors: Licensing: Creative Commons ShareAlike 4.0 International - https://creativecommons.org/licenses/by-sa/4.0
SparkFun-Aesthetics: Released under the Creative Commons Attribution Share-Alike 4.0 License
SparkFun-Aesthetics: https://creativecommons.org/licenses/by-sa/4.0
